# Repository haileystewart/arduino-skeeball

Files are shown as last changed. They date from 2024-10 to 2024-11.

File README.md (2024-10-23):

# Pi-Arduino Skeeball
An interactive skeeball-inspired game using Arduino for sensors and lighting, and Raspberry Pi for managing the scoreboard and game logic.

## Features:
- Real-time scoring with light and sound effects
- Customizable game modes
- Easy to set up with Arduino and Raspberry Pi

## Getting Started
1. Follow the [Setup Instructions](docs/setup.md) to wire the hardware.
2. Upload the Arduino code found in `/src/arduino/`.
3. Run the Python scoreboard script on your Raspberry Pi.

## Game Play
Players bounce ping pong balls into targets, scoring points tracked by the Raspberry Pi. Sound and light effects trigger when targets are hit.

https://www.instructables.com/Wooden-Skeeball-Game/
https://www.instructables.com/Automatic-Scoring-for-a-Small-Skee-Ball-Game/
https://www.instructables.com/Homemade-Skee-Ball-Game/

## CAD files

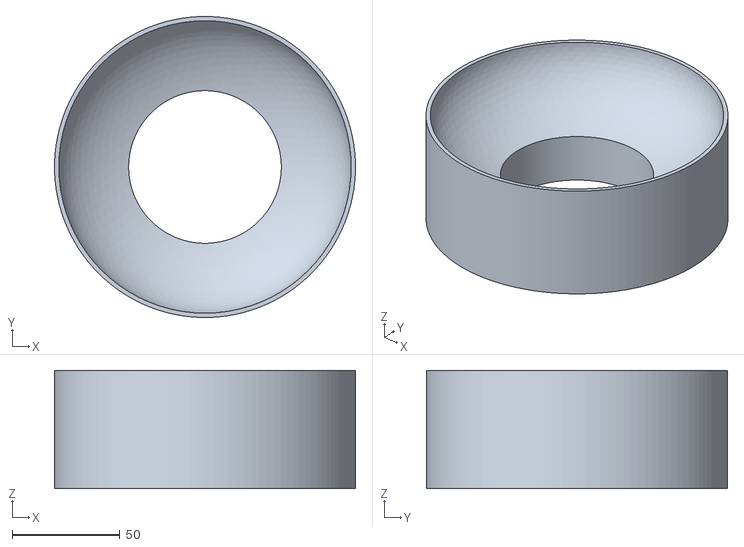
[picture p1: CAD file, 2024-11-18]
3d/70-bowl.stl
140.0 x 140.0 x 55.0

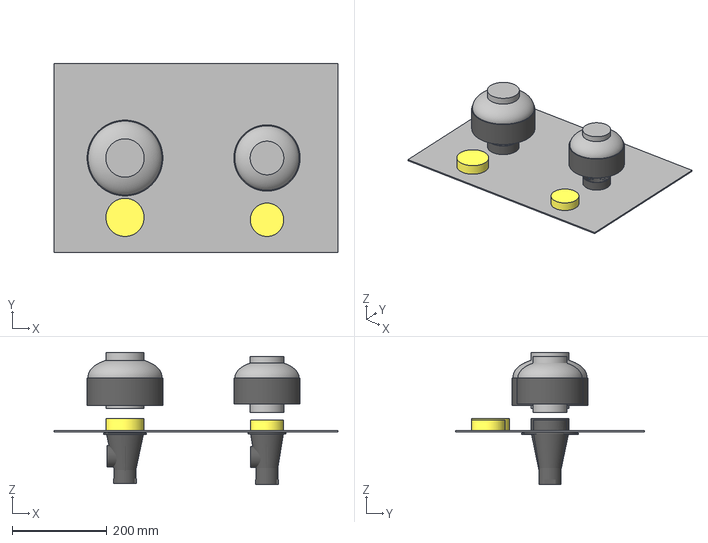
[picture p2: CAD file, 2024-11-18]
3d/top-bowls.3mf
600.0 x 400.0 x 279.5 mm

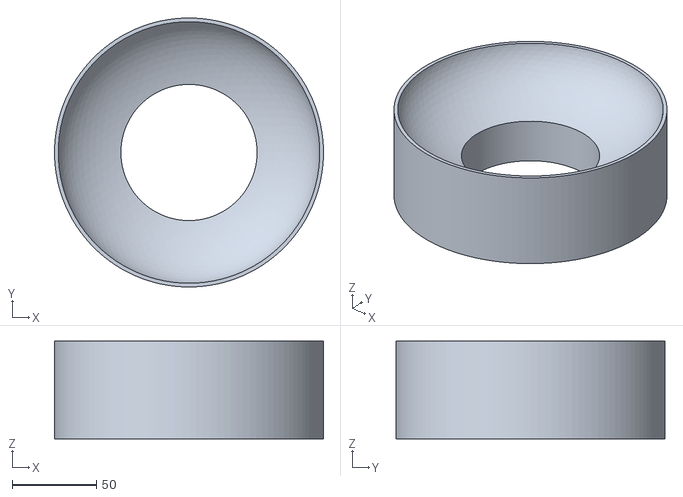
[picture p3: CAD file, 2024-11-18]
3d/80-bowl.stl
160.0 x 160.0 x 58.0

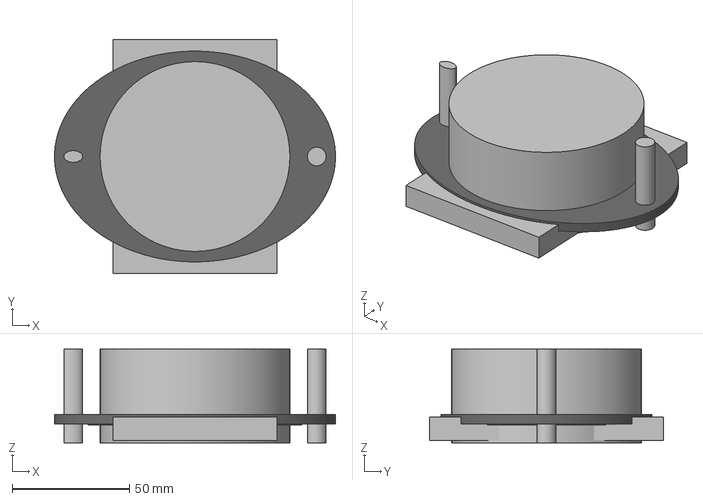
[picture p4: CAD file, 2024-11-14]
3d/80-extender-ring.3mf
120.0 x 100.0 x 40.0 mm

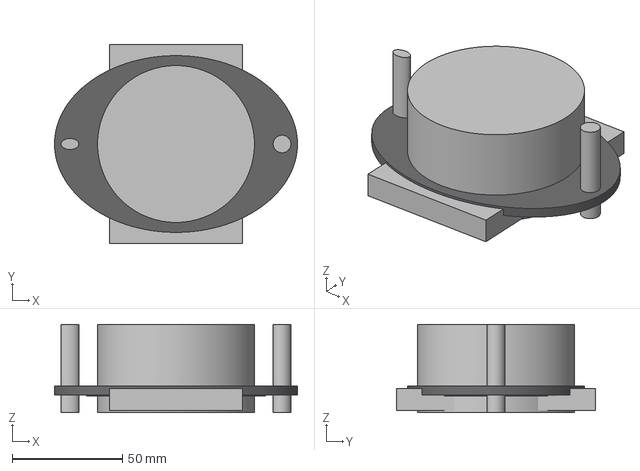
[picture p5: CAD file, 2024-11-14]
3d/70-extender-ring.3mf
110.0 x 90.0 x 40.0 mm

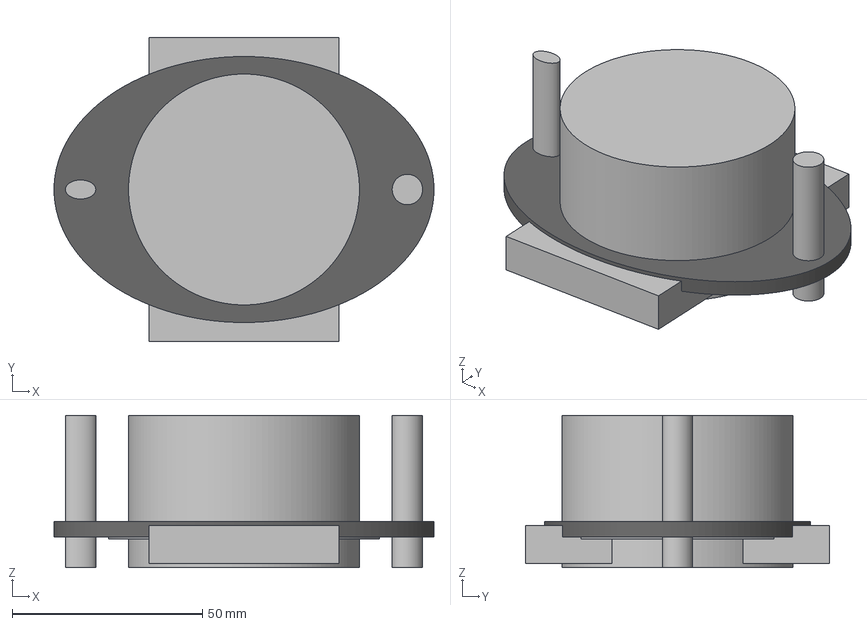
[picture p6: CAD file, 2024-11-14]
3d/60-extender-ring.3mf
100.0 x 80.0 x 40.0 mm

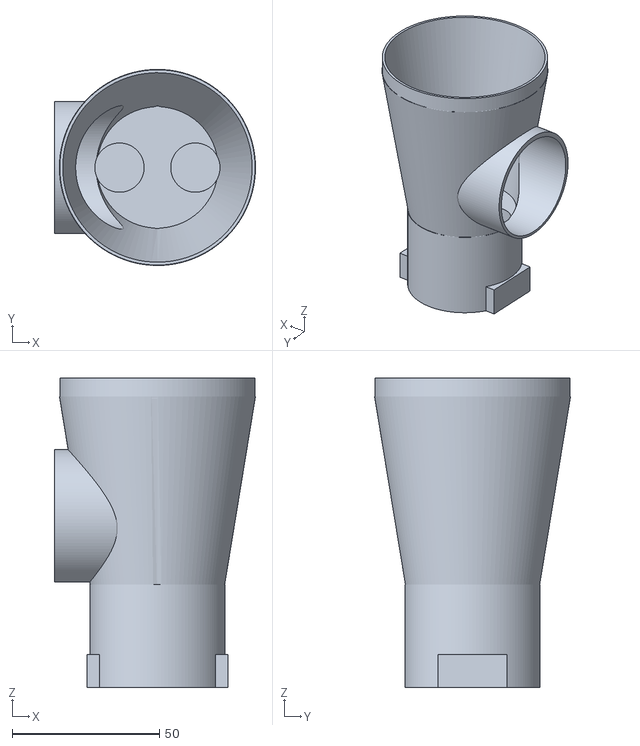
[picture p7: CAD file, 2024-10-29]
3d/70-ultra-sensor-2.stl
68.3 x 68.3 x 109.1

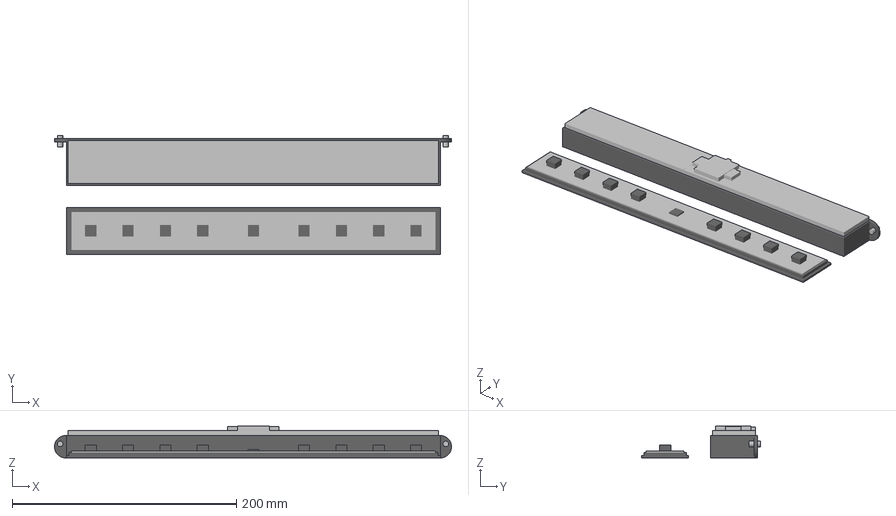
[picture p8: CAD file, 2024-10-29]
3d/top-display.3mf
353.7 x 105.9 x 28.5 mm

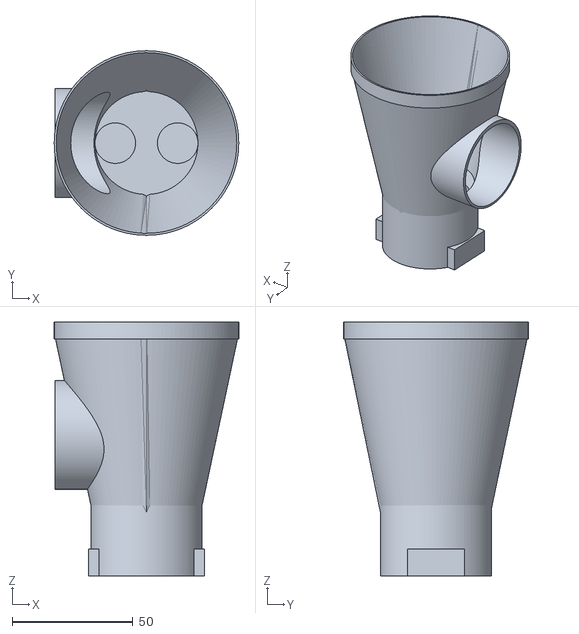
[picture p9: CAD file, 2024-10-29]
3d/80-ultra-sensor-2.stl
76.3 x 76.3 x 105.0

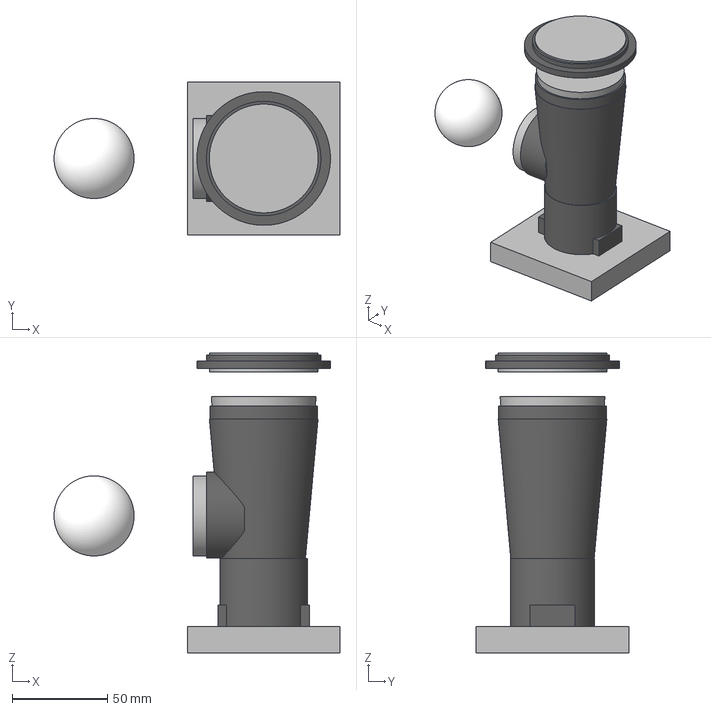
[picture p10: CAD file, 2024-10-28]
3d/60-ultra-sensor.3mf
149.9 x 80.0 x 157.3 mm

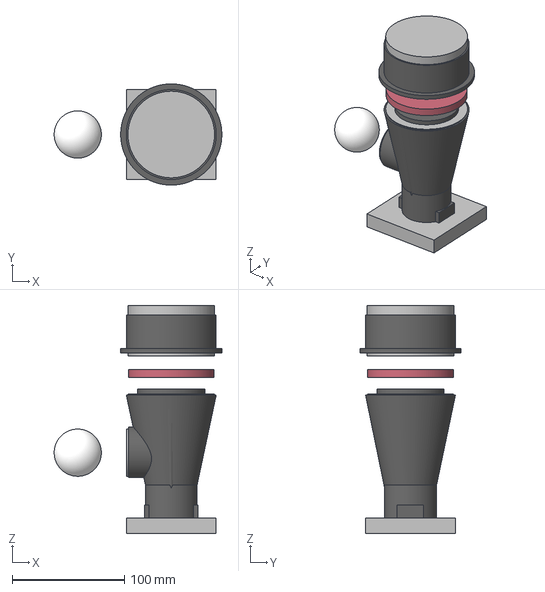
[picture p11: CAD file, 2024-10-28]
3d/80-ultra-sensor.3mf
149.1 x 90.0 x 202.8 mm

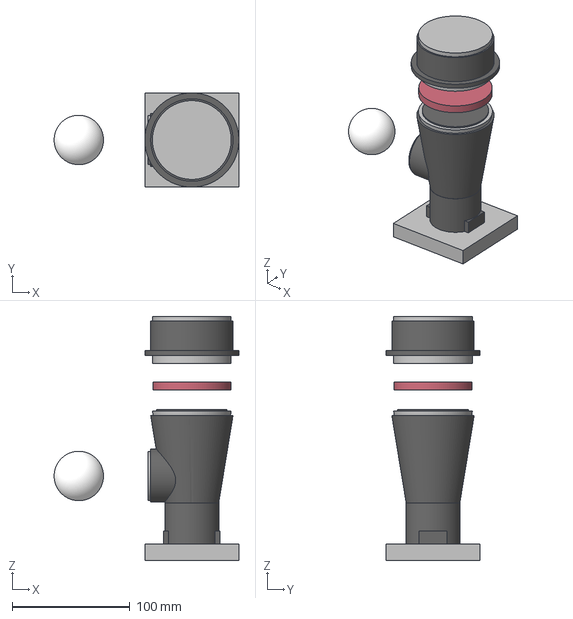
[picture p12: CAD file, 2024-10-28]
3d/70-ultra-sensor.3mf
157.1 x 80.0 x 207.5 mm

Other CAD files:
3d/60-extender-ring.stl
3d/60-ultra-sensor.stl
3d/70-extender-ring.stl
3d/80-extender-ring.stl
3d/top-display.stl

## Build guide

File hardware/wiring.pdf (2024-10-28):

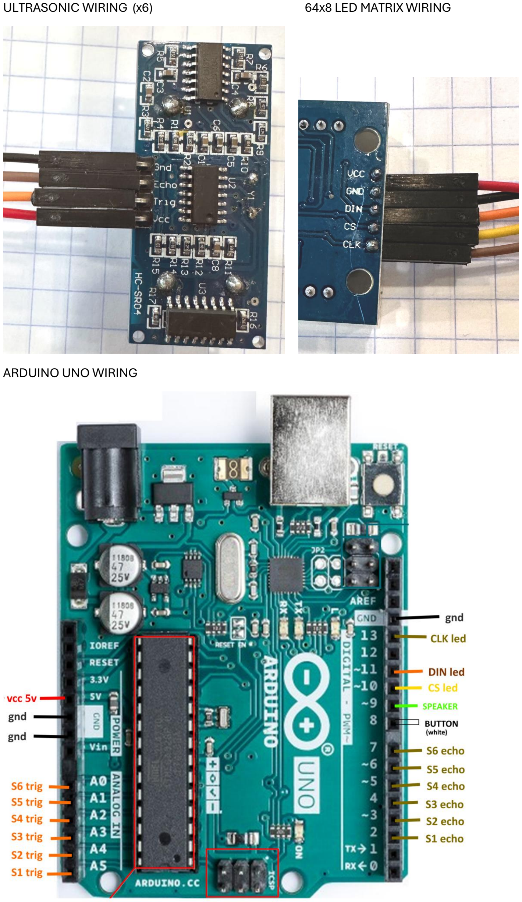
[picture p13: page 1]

ULTRASONIC WIRING (x6) | 64x8 LED MATRIX WIRING

ARDUINO UNO WIRING

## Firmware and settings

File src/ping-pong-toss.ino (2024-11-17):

#include <MD_MAX72xx.h>
#include <SPI.h>
#include "sensor.h"
#include "tone.h"

// game defines
#define ULTRASONIC_SENSORS  6
#define DEBUG_SENSOR        -1
#define WAIT_BETWEEN_BALLS  1000
#define BUTTON_PIN          8

// led matrix definitions
#define HARDWARE_TYPE       MD_MAX72XX::FC16_HW
#define DATA_PIN            11
#define CLK_PIN             13
#define CS_PIN              10
#define LED_MODULES         8   // there are 8 8x8 modules
#define LED_BRIGHTNESS      10  // brightness level is 0..15

MD_MAX72XX matrix = MD_MAX72XX(HARDWARE_TYPE, DATA_PIN, CLK_PIN, CS_PIN, LED_MODULES);

Tone gameTone;

int  score        = 0;
int  highScore    = 0;
int  balls        = 9;
bool gameRunning  = false;
int  cycle        = 0;
int  cycleDelay   = 0;

// list of ultrasonic sensors
Sensor sensors[ULTRASONIC_SENSORS] =
{
  Sensor(A5, 2, 300, 100, 110),
  Sensor(A4, 3, 300, 200, 220),
  Sensor(A3, 4, 300, 400, 330),
  Sensor(A2, 5, 300, 500, 440),
  Sensor(A1, 6, 300, 1000, 660),
  Sensor(A0, 7, 300, 1000, 660)
};

// 0-9 character binary map
const uint8_t numbers[10][8] = 
{
  {0b00000000, 0b01111111, 0b01000001, 0b01000001, 0b01000001, 0b01000001, 0b01111111, 0b00000000}, // 0
  {0b00000000, 0b00000000, 0b01000000, 0b01000001, 0b01111111, 0b01000000, 0b01000000, 0b00000000}, // 1
  {0b00000000, 0b01111001, 0b01001001, 0b01001001, 0b01001001, 0b01001001, 0b01001111, 0b00000000}, // 2
  {0b00000000, 0b01001001, 0b01001001, 0b01001001, 0b01001001, 0b01001001, 0b01111111, 0b00000000}, // 3
  {0b00000000, 0b00001111, 0b00001000, 0b00001000, 0b00001000, 0b00001000, 0b01111111, 0b00000000}, // 4
  {0b00000000, 0b01001111, 0b01001001, 0b01001001, 0b01001001, 0b01001001, 0b01111001, 0b00000000}, // 5
  {0b00000000, 0b01111111, 0b01001001, 0b01001001, 0b01001001, 0b01001001, 0b01111001, 0b00000000}, // 6
  {0b00000000, 0b00000001, 0b00000001, 0b00000001, 0b00000001, 0b00000001, 0b01111111, 0b00000000}, // 7
  {0b00000000, 0b01111111, 0b01001001, 0b01001001, 0b01001001, 0b01001001, 0b01111111, 0b00000000}, // 8
  {0b00000000, 0b01001111, 0b01001001, 0b01001001, 0b01001001, 0b01001001, 0b01111111, 0b00000000}  // 9
};

// display 0-9 number at matrix position 0-7
void displayNum(int position, int num)
{
  position = (position % 8) * 8;

  for (int i = 0; i < 8; i++)
    matrix.setColumn(63 - (position + i), numbers[num][i]);
}

// display character on led at position
void displayChar(int position, char c, bool left=false) 
{
  uint8_t charBuffer[8];  // Buffer to hold the character columns
  uint8_t width = matrix.getChar(c, sizeof(charBuffer), charBuffer);  // Retrieve the bitmap for the character
  uint8_t start = left?62:30;

  for (int i = 0; i < 8; i++)
  {
    uint8_t p = start - (position + i);
    if (p >= 0 && p <= (start+1))
    {
      uint8_t b = (i < width)?charBuffer[i]:0;
      matrix.setColumn(p, b);
    }
  }
}

void displayString(String data, bool left=false)
{
  matrix.control(0, LED_MODULES-1, MD_MAX72XX::UPDATE, MD_MAX72XX::OFF);

  uint8_t p = 0;
  for(int i=0; i<data.length(); i++)
  {
    displayChar(p,data[i], left);
    p += 8;
  }

  matrix.control(0, LED_MODULES-1, MD_MAX72XX::UPDATE, MD_MAX72XX::ON);
}

void displayScore(int s, int b = -1)
{
  matrix.control(0, LED_MODULES-1, MD_MAX72XX::UPDATE, MD_MAX72XX::OFF);

  if (b >= 0)
  {
    // remaining balls
    displayNum(1, (b / 10) % 10);
    displayNum(2, b % 10);
  }

  // each digit at a time
  displayNum(4, s / 1000);
  displayNum(5, (s / 100) % 10);
  displayNum(6, (s / 10) % 10);
  displayNum(7, s % 10);

  matrix.control(0, LED_MODULES-1, MD_MAX72XX::UPDATE, MD_MAX72XX::ON);
}

void setup() 
{
  Serial.begin(115200);
  delay(500);

  pinMode(BUTTON_PIN, INPUT_PULLUP);

  // configure sensor pins
  for(int i = 0; i < ULTRASONIC_SENSORS; i++)
    sensors[i].setup();

  // led matrix setup
  matrix.begin();
  matrix.control(MD_MAX72XX::INTENSITY, LED_BRIGHTNESS);
  matrix.clear();
  matrix.update();
}

void loop() 
{
  if (gameRunning)
  {
    // cycle through all sensors
    for (int i=0; i < ULTRASONIC_SENSORS; i++)
    {
      unsigned long currentMillis = millis();

      // debounce logic
      if (currentMillis > sensors[i].nextDetect)
      {
        unsigned long distance = sensors[i].getDistance();

        // write out to serial monitor sensor distance
        if (i == DEBUG_SENSOR)
          Serial.println(distance);

        if (distance <= sensors[i].detectRange)
        {
          // wait before we can rescan this sensor)
          for(int j=0;j<ULTRASONIC_SENSORS;j++)
            if (sensors[j].triggerPin == sensors[i].triggerPin)
              sensors[j].nextDetect = currentMillis + WAIT_BETWEEN_BALLS;

          gameTone.setTone(sensors[i].tone);
          
          score += sensors[i].points;  // add and display score
          balls--;  // one less ball

          if (score > highScore)
            highScore = score;

          displayScore(score, balls);

          // if it's our last ball then game is over
          if (balls <= 0)
          {
            gameRunning = false;
            cycle = 9;
          }
        }
      }
    }
  }
  else 
  {
    switch(cycle)
    {
      case 0:
        displayString("PING    ", true);
        cycleDelay = 500;
        cycle++;
        break;

      case 1:
        displayString("    PING", true);
        cycleDelay = 500;
        cycle++;
        break;

      case 2:
        displayString("PONG    ", true);
        cycleDelay = 500;
        cycle++;
        break;

      case 3:
        displayString("    PONG", true);
        cycleDelay = 500;
        cycle++;
        break;

      case 4:
        displayString("TOSS    ", true);
        cycleDelay = 500;
        cycle++;
        break;

      case 5:
        displayString("    TOSS", true);
        cycleDelay = 500;
        cycle++;
        break;

      case 6:
        displayString("LAST", true);
        displayScore(score);
        cycleDelay = 1500;
        cycle++;
        break;

      case 7:
        displayString("HIGH", true);
        displayScore(highScore);
        cycleDelay = 1500;
        cycle++;
        break;

      case 8:
        displayString("PUSH-GO-", true);
        cycleDelay = 2000;
        cycle = 0;
        break;

      case 9:
        displayString("GAMEOVER", true);
        cycleDelay = 2000;
        cycle = 6;
        break;
    }

    bool pressed = false;
    unsigned long expiry = millis() + cycleDelay;
    while(millis() < expiry)
    {
      if (digitalRead(BUTTON_PIN) == LOW)
      {
        pressed = true;
        break;
      }

      delay(10);
    }

    if (pressed)
    {
      gameTone.setTone(0);

      score = 0;
      balls = 9;
      gameRunning = true;

      displayString("-  -", true);
      displayScore(score, balls);
    }
  }

  gameTone.loop();
}

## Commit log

2024-10-16 Update skeeball-arduino.ino
    Added ultrasonic sensors and led matrix display. Need to add the MD_MAX72XX library (majicDesigns) using the library manager to get it to build.
2024-10-19 Update skeeball-arduino.ino
    Updated with actual hardware and gameplay
2024-10-20 Update skeeball-arduino.ino
    Reconfigured pins and added comments
2024-10-20 Added wiring diagram
2024-10-23 Added .3MF and .STL led matrix case/bracket
    [led-matrix-box.3mf, led-matrix-box.stl]
2024-10-25 Added 70 and 80 mm sensor mounts
    [ultrasonic-sensor-70.stl, ultrasonic-sensor-80.stl]
2024-10-29 Initial check-in
    Separating out display and sensor hardware implementations
